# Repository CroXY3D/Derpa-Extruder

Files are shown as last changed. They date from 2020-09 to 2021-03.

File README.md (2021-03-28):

# Derpa Extruder
 
A lightweight extruder using a BMG + a 70g LDO Nema14 motor with integrated 10T pinion.  Printed parts total 4g.  Total weight of Derpa + Nema 14 Motor + BMG is 140g.  A BMG + 25mm pancake is approx 220g.

The 10 tooth pinion on the LDO motor along with the BMG gear gives a 5.1:1 gear ratio, which is enough to push 14mm^3/s through an e3dv6 with 0.4mm nozzle.  It should be able to push more through a Volcano.

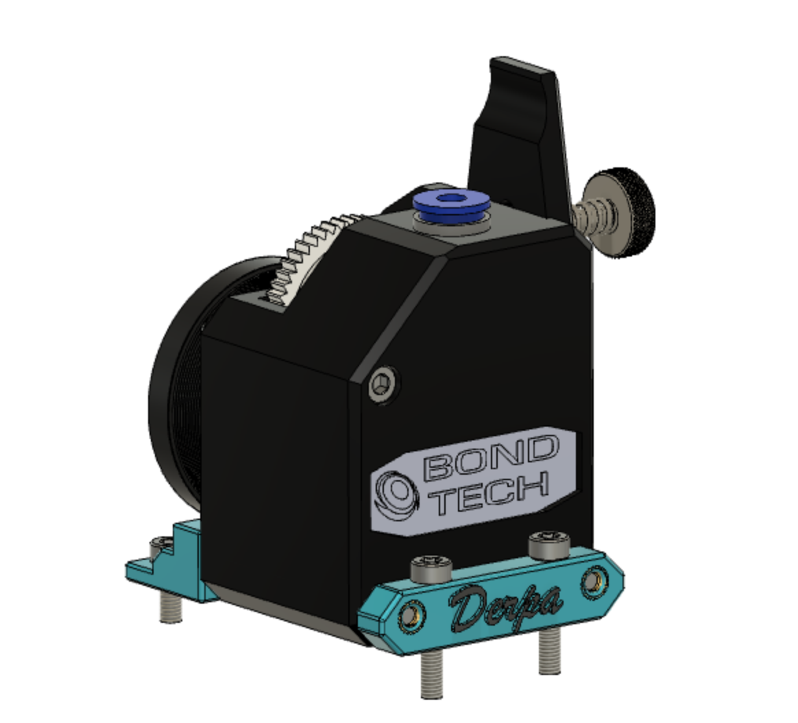
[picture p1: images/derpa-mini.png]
Image of Derpa Mini
 
 
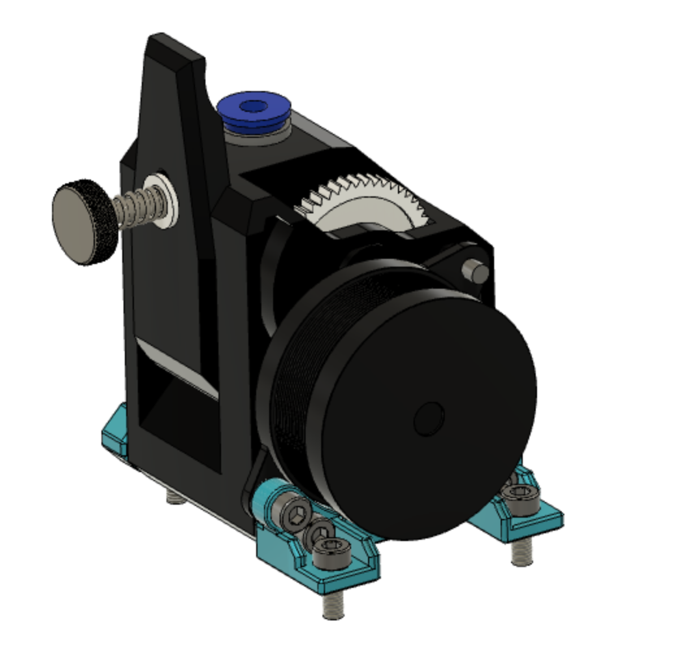
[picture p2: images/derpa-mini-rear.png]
Image of Derpa Mini
  
 
 [Uses this 70g LDO Nema14 motor](https://www.printedsolid.com/products/ldo-nema-14-motor-ldo-36sth17-1004ahg?variant=32690500370517)

Note, you may have to file off a super tiny bit of the lower ear as it can interfere with the screw holding the BMG together.  

STEP and Fusion 360 archive provided. 

# BOM
  - Qty 1 BMG
  - Qty 1 [LDO Nema 14 Motor](https://www.printedsolid.com/products/ldo-nema-14-motor-ldo-36sth17-1004ahg?variant=32690500370517)
  - Qty 1 M3x35 SHCS
  - Qty 2 M3x45 SHCS
  - Qty 1 M3x6 SHCS
  - Qty 4 M3x? Screws to mount.

# RRF 3 Settings
```
M906 E300  ; 300 mA current (try 350)
M92 E703   ; steps/mm
M201 E100  ; Accel, Not tuned
M203 E1800 ; Max Speed
M566 E1000 ; 1000 RRF InstantDv
```
# Discord for Derpa-Extruder and CroXY

[Discord Invite](https://discord.gg/ryj6wyx)

# Remixes
bartolomeus has made an [excellent remix of Derpa](https://www.thingiverse.com/thing:4692392) for the Sovol SV01 printer.  His approach uses a ring which attaches the motor to a BMG.  The BMG face mounts to the rest of the toolhead.  It could easily be adapted to a number of other printers.

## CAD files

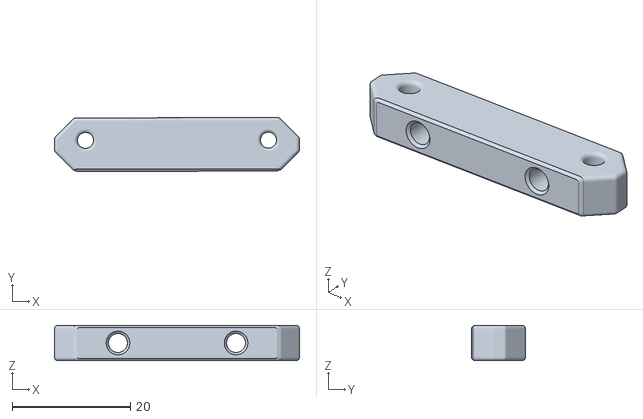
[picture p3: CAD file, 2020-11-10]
STLs/Derpa_Front_No_Logo.stl
41.5 x 9.13 x 6.00

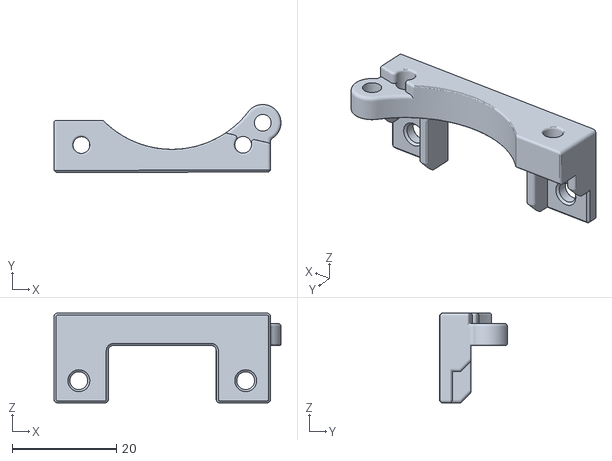
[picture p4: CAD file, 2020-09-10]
STLs/Derpa Rear.stl
43.5 x 13.0 x 17.2

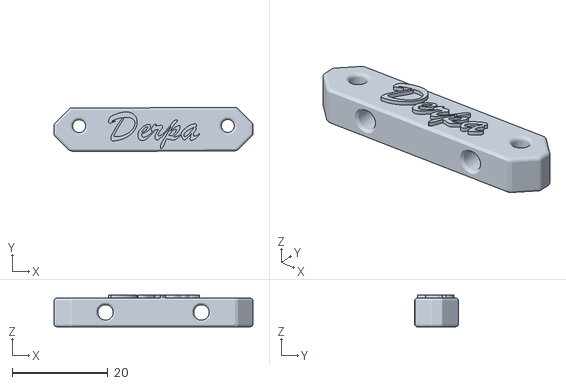
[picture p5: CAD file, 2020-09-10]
STLs/Derpa_Front.stl
41.5 x 9.13 x 6.60

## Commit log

2020-09-10 images and stls
    [Derpa Rear.stl, Derpa_Front.stl]
2020-11-10 No logo version
    [Derpa_Front_No_Logo.stl]
